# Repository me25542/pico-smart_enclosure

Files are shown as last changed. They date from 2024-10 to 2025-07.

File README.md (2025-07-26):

# pico-smart_enclosure
### Automatic active temperature control and lighting for a 3d printer enclosure.
Uses a raspberry Pi Pico connected to the printer via I2C to provide **automatic** active temperature control and full control of other enclosure functions via gcode (M260). 
Also gives full control via an OLed screen UI.

## Features
- **Automatic active temperature control**
- **Direct communication with the printer** (via I2C)
- **Smooth PWM lighting control**
- **Power loss recovery** (will save setting changes and state on power loss)
- **UI via OLed**
- Print name display while printing
- Fan kickstarting
- PWM fan speed control
- Printer-controllable max fan speed
- Motorized fan flap control
- Print done notification (light turns on)
- Use of the standby capabilities on ATX PSUs to save power
- Uses both cores in the pico for smoother real-time operation
- Highly customizable
- Light turns on when the door opens (if setting enabled)
- Control via:
    - UI - full control (except for print name), plus settings
    - M260 gcode commands (printer) - full control
    - USB connected computer - partial control (all but print name)
    - Two quick-acess buttons - changing light state and setting mode to cooldown only
- **Safety** features:
    - Fans and heaters turn off when door open
    - Sensor connection status is regularly checked
    - Sensor data is checked for plausibility (is it way to low, etc.)
    - Temperature exceeding set thresholds will cause shutdown (see below)
    - Will enter a safe "error" state if anything is wrong (invalid printer command, sensor disconnected, temp exceeds set bounds, etc.)
        - Turns off heaters
        - Turns off fans
        - Turns off lights
        - Turns off the power supply
        - Stops communication with printer
        - Sends data about the error via USB every 30 seconds, indefinitely

## To use
- **If you don't need to change anything in the code (if your hardware is the same as mine):**
	- Double check your wiring
        - Couldn't hurt, for what mine looks like see the wiring diagram below
        - Your switches can be either `NO` or `NC`, the code will detect this
    - **Ensure that whenever you upload a new version, the door is open (no switches are pressed)**
	- Plug the Raspberry Pi Pico into your computer while holding down the BOOTSEL button, copy [the latest .uf2 file](https://github.com/me25542/pico-smart_enclosure/releases) to the pico
	- Enjoy!
- **If you want to customize things in the code:**
	- I recommend Using Arduino IDE, as that is what I used and I know it works
	- Install [this](https://github.com/earlephilhower/arduino-pico) board in Arduino IDE
	    - The link has good instructions, just scroll down a bit
	- Install all dependencies (see documentation)
	- Download the files in "src/Printer_enclosure_firmware" and open them in Arduino IDE
	- Change any values as needed, depending on your setup
	- Double check your wiring (couldn't hurt, for what mine looks like see the wiring diagram below)
	- Upload the code to your Pico (see above)
	- Enjoy!

- **For wiring diagram, BOM, etc., see the documentation**

## Printer compatibility
**This design is compatible with any printer that supports [M260](https://reprap.org/wiki/G-code#M260:_i2c_Send_Data) gcode commands and has an I2C bus that you can connect to.**

The only printers that I am *certain* will work with this are the Original Prusa MK4-series printers (I made this for my MK4), as their Xbuddy board has an I2C connector that is unused. (a female 4-pin Molex Click-Mate if you want to buy a cable to fit)

**Known compatible printers:**
- Prusa MK4(s)
- Prusa MK3.9(s)
- Prusa MK3.5(s)

However, many other printers *might* have I2C connectors, so it's worth checking yours. If you find other printers that are compatible, please let me know!

A raspberry Pi might also work (they have I2C) if you are using one for Octoprint or Klipper already, with a bit of modification.

## Contribution
If you want to contribute in any way, feel free to do so!

Whether it's reporting bugs or writing code, your contributions will be helpful.

### Ideas for features to add
- Thermal runaway protection
    - protect heaters from thermal runaway
- Audible notification for print done
    - Play a small chime or sound when the print is set to done
- Support for basic control through printer GPIO pins (for printers without I2C)
    - Have a small number of pins be able to, say, set the temperature to one of two states
    - Cut out any unneeded functionality (like setting the lights, fine temperature control, etc.)
- Anything else you can think of!
    - If you can, implement it!
    - If you can't, raise an issue requesting the feature

Thank you for any and all contributions!

---

**OK, I saved the story for the end 😉.**

I couldn't find code for a smart printer enclosure that had all the features I wanted. 
Mainly, I wanted something that was automatic; I didn't want to have to set fans, heaters, etc. *every single print**. 
So, I spent a lot of time making this. 
I believe it is the most fully featured codebase for a 3d printer enclosure you could find, mainly because I couldn't find a more fully featured one.

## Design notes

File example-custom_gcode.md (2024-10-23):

## example custom gcode:

(compatible with any PrusaSlicer-based slicer)
- Prusa Slicer
- Bambu Studio
- Orca Slicer
- Super Slicer

This start gcode is based off of commands compatible with v1.1.0

List of compatible versions:
- 1.1.0
- 1.1.1
- 1.2.0

It should also be compatible with any v1.x version later than this

### Start gcode:

(add at the *verry* start of your printer's start gcode)

```
; start of my custom stuff:
M260 A8 ; set adress to 8
M260 B3 ; set enclosure mode to printing
M260 B5 ; set print not done
{if filament_type[initial_tool]=="PLA"}
M260 B15 ; set target enclosure temp to 15deg C
{elsif filament_type[initial_tool]=="PETG"}
M260 B30 ; set target enclosure temp to 30deg C
M260 B102 ; set max enclosure fan speed to 50%
{elsif filament_type[initial_tool]=="ASA"||filament_type[initial_tool]=="ABS"}
M260 B50 ; set target enclosure temp to 50deg C
M260 B100 ; set max enclosure fan speed to 0%
{elsif filament_type[initial_tool]=="FLEX"}
M260 B25 ; set target enclosure temp to 25deg C
{elsif filament_type[initial_tool]=="PC"}
M260 B50 ; set target enclosure temp to 50deg C
M260 B100 ; set max enclosure fan speed to 0%
{elsif filament_type[initial_tool]=="PA"||filament_type[initial_tool]=="NYLON"}
M260 B50 ; set target enclosure temp to 50deg C
M260 B100 ; set max enclosure fan speed to 0%
{endif}
M260 S ; send the current buffer
; end of my custon stuff
```

### End gcode

(add at the *verry* end of your printer's end gcode)

```
; start of my custom stuff:
M260 A8 ; set adress to 8
M260 B20 ; set target enclosure temp to 20deg C
M260 B2 ; set enclosure mode to cooldown
M260 B4 ; set print done
M260 S ; send the current buffer
; end of my custom stuff
```

### See also:

[RepRap - M260](https://reprap.org/wiki/G-code#M260:_i2c_Send_Data)

[Macros | Prusa knowledge base](https://help.prusa3d.com/article/macros_1775)

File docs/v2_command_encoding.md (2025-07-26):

# I2C command encoding

The encoding of commands to the enclosure into bytes sent via I2C is a bit more complicated in v2 than in v1. 
Instead of a rudimentary system where each possible byte is mapped to a command (e.g. `46` sets the target enclosure temp to 46 degrees), 
commands are encoded as a series of bytes. Each v2 command consists of at least 3 bytes: the command type, the number of bytes, and the data. 
The command structure is like this (first sent bytes on the left):

`command type`  |`number of data bytes` |`data bytes`
---             |---                    |---
^ first sent    |^ second sent          |^ last sent

The command type indicates *what* is being set. 
Currently, the only valid command types are `0xFF` to `0xF7` (`255` to `247`). 
These set different things:

Hex     |Dec    |Command type
---     |---    |---
`0xFF`  |`255`  |mode
`0xFE`  |`254`  |set temp
`0xFD`  |`253`  |print done
`0xFC`  |`252`  |max fan speed
`0xFB`  |`251`  |light state
`0xFA`  |`250`  |print name
`0xF9`  |`249`  |control mode
`0xF8`  |`248`  |heaters
`0xF7`  |`247`  |fan

The number of data bytes indicates how many data bytes are contained in the command
(e.g. if there are two data bytes this byte would be `0x02` (`2`), eighteen data bytes would make this `0x12` (`18`), etc.).

The data bytes contain the actual command data. 
What this data does / how it is encoded depends on the command type.

## Data byte actions by command type:

### Mode (`0xFF` hex, `255` dec):

Hex     |Dec    |Action
---     |---    |---
`0x00`  |`0`    |mode to error
`0x01`  |`1`    |mode to standby
`0x02`  |`2`    |mode to cooldown
`0x03`  |`3`    |mode to printing
(other) |(other)|ignored

<br>

### Set temp (`0xFE` hex, `254` dec):

Hex     |Dec    |Action
---     |---    |---
`0x00`  |`0`    |set temp to 0 (deg. c.)
`0x01`  |`1`    |set temp to 1
...     |...    |...
`0x4A`  |`74`   |set temp to 74
`0x4B`  |`75`   |set temp to 75
(other) |(other)|ignored

<br>

### Print done (`0xFD` hex, `253` dec):

Hex     |Dec    |Action
---     |---    |---
`0x00`  |`0`    |print not done
`0x01`  |`1`    |print done
(other) |(other)|ignored

<br>

### Max fan speed (`0xFC` hex, `252` dec):

Hex     |Dec    |Action
---     |---    |---
`0x00`  |`0`    |max fan speed to 0/255
`0x01`  |`1`    |max fan speed to 1/255
...     |...    |...
`0xFE`  |`254`  |max fan speed to 254/255
`0xFF`  |`255`  |max fan speed to 255/255

<br>

### Light state (`0xFB` hex, `251` dec):

Hex     |Dec    |Action
---     |---    |---
`0x00`  |`0`    |lights on
`0x01`  |`1`    |lights off
`0x02`  |`2`    |lights change
(other) |(other)|ignored

<br>

### Print name (`0xFA` hex, `250` dec):

This one is a bit different. Basically, each data byte represents one ASCII-encoded character in the print name. 
Each of these characters are added, one at a time, to the print name in place of the first `NULL`. 
The print name is full of `NULL`s when empty, so basically each character is added to the end of the part of the name that is already there.

#### Notes: 

The print name is cleared after each print automatically (when the mode returns to `standby`).
The print name has a 256-character limit, characters added after it is full will change the last character.

<br>

### Control mode (`0xF9` hex, `249` dec):

Hex     |Dec    |Action
---     |---    |---
`0x00`  |`0`    |undefined; do not use
`0x01`  |`1`    |control mode to temperature
`0x02`  |`2`    |control mode to manual
(other) |(other)|ignored

<br>

### Heaters (`0xF8` hex, `248` dec):

Hex     |Dec    |Action
---     |---    |---
`0x00`  |`0`    |heater off
`0x01`  |`1`    |heater on
(other) |(other)|ignored

#### Note:

Do not use unless the control mode is set to manual, otherwise behavior is undefined

<br>

### Fan (`0xF7` hex, `247` dec):

Hex     |Dec    |Action
---     |---    |---
`0x00`  |`0`    |fan to 0/255
`0x01`  |`1`    |ignored
`0x02`  |`2`    |fan to 2/255
`0x03`  |`3`    |ignored
...     |...    |...
`0xFC`  |`252`  |fan to 252/255
`0xFD`  |`253`  |ignored
`0xFE`  |`254`  |fan to 254/255
`0xFF`  |`255`  |ignored

#### Note:

If the least significant bit is `1`, the byte will be ignored

<br>

### Gcode examples:

#### Setting mode to `printing`:

<details>
<summary> expand </summary>

```
M260 A8 ; Address 8
M260 B255 ; Mode
M260 B1 ; 1 Byte
M260 B3 ; Printing
M260 S ; Send buffer
```

</details>

---

#### Setting a long name:

<details> 
<summary> expand </summary>

```
M260 A8 ; Address 8

; First I2C transaction (32 bytes total)
; Send the first part of the name (30 bytes)
M260 B250 ; Print name
M260 B30 ; 30 Bytes

M260 B84 ; 'T'
M260 B104 ; 'h'
M260 B105 ; 'i'
M260 B115 ; 's'
M260 B32 ; ' '
M260 B105 ; 'i'
M260 B115 ; 's'
M260 B32 ; ' '
M260 B97 ; 'a'
M260 B32 ; ' '
M260 B118 ; 'v'
M260 B101 ; 'e'
M260 B114 ; 'r'
M260 B121 ; 'y'
M260 B32 ; ' '
M260 B108 ; 'l'
M260 B111 ; 'o'
M260 B110 ; 'n'
M260 B103 ; 'g'
M260 B32 ; ' '
M260 B110 ; 'n'
M260 B97 ; 'a'
M260 B109 ; 'm'
M260 B101 ; 'e'
M260 B32 ; ' '
M260 B116 ; 't'
M260 B111 ; 'o'
M260 B32 ; ' '
M260 B116 ; 't'
M260 B101 ; 'e'

M260 S ; Send buffer

; Second I2C transaction (27 bytes total)
; Send the remaining part of the name (25 bytes)
M260 B250 ; Print name
M260 B26 ; 26 Bytes

M260 B115 ; 's'
M260 B116 ; 't'
M260 B32 ; ' '
M260 B115 ; 's'
M260 B116 ; 't'
M260 B117 ; 'u'
M260 B102 ; 'f'
M260 B102 ; 'f'
M260 B46 ; '.'
M260 B32 ; ' '
M260 B84 ; 'T'
M260 B101 ; 'e'
M260 B115 ; 's'
M260 B116 ; 't'
M260 B44 ; ','
M260 B32 ; ' '
M260 B116 ; 't'
M260 B101 ; 'e'
M260 B115 ; 's'
M260 B116 ; 't'
M260 B44 ; ','
M260 B32 ; ' '
M260 B116 ; 't'
M260 B101 ; 'e'
M260 B115 ; 's'
M260 B116 ; 't'

M260 S ; Send buffer
```

</details>

---

#### Manually turning heater on:

<details>
<summary> expand </summary>

```
M260 A8 ; Address 8
M260 B249 ; Control mode to manual
M260 B1 ; 1 Byte
M260 B248 ; Heater
M260 B1 ; Heater on
M260 S ; Send buffer
```

</details>

<br>

## Notes:

**On command length / why this encoding:**

Many commands only require one data byte, but some (like setting the print name) require more. 
Hence the byte indicating the number of data bytes.

---

**On addresses:**

The I2C address of the enclosure by default is `0x08` in hex, or `8` in dec. This can be changed by modifying a macro in the source code.

---

**On v1 compatibility:**

To maintain compatibility with v1, if the `command type` byte is in the range of `0x00` - `0x68` (`0` - `104`), it will be parsed as if it is a v1 command.
v1 commands were only one byte long, so if this is the case the next command is assumed to start with the next byte.
This means that valid v1 commands *are* still fully supported, and can be mixed with v2 commands in a given transmission.
However, it is recommended to use only v2 commands, as support for v1 commands is not guaranteed indefinitely.

---

**On maximum transmission length:**

The Marlin core used by the Prusa Buddy firmware has a limited I2C buffer size of 32 bytes; if you are sending many or long commands you may need to split them into multiple transmissions.
Additionally, the enclosure code has only a 32-byte primary buffer for incoming data, so longer transmissions wouldn't work. 
However, this buffer is flushed to a 256-byte circular buffer nearly immediately, so consecutive commands of up to 32 bytes should be fine. 
If you need more than 32 bytes, split it into multiple transmissions.

---

**If you still have questions, or this document is incomplete, please submit an issue.**

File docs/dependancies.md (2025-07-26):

## This program has several dependencies you will need to install if you want to compile it yourself:

**Mainly, you will need to install the [earlephilhower / Arduino-pico core](https://github.com/earlephilhower/arduino-pico).** This provides both the ability to compile code for the Pico, and several dependencies like:
  - stdlib
  - Wire
  - Servo
  - EEPROM
  - mutex

---

[How to install the Arduino-pico core](https://github.com/earlephilhower/arduino-pico/blob/master/docs/install.rst)

---

**Other libraries that need to be installed include:**
- [Adafruit MCP9808](https://github.com/adafruit/Adafruit_MCP9808_Library)
- [Adafruit GFX Library](https://github.com/adafruit/Adafruit-GFX-Library)
- [Adafruit SSD1306](https://github.com/adafruit/Adafruit_SSD1306)
- [Bounce2](https://github.com/thomasfredericks/Bounce2)
- Some of these have dependencies of their own, just select "install all" when prompted in arduino IDE

---

Happy compiling!

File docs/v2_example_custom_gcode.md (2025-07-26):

## v2 example custom gcode:

(compatible with any PrusaSlicer-based slicer)
- Prusa Slicer
- Bambu Studio
- Orca Slicer
- Super Slicer

**This example gcode is based off of commands compatible with v2.0.0_rc1 (internal, prerelease)**

List of compatible versions:
- v2.0.0_rc1 (internal, prerelease)
- v2.x

It should also be compatible with any v2.x versions in the future

### Start gcode:

(add at the *very* start of your printer's start gcode)

<details>

<summary> expand </summary>

```
; start of my custom stuff:
M260 A8 ; set address to 8
M260 B255 ; setting: mode
M260 B1 ; 1 byte
M260 B3 ; mode: printing
M260 B253 ; setting: print done
M260 B1 ; 1 byte
M260 B0 ; print done: false
{if filament_type[initial_tool]=="PLA"}
M260 B254 ; setting: enclosure temp
M260 B1 ; 1 byte
M260 B15 ; enclosure temp: 15deg
M260 S ; send the current buffer
{elsif filament_type[initial_tool]=="PETG"}
M260 B254 ; setting: enclosure temp
M260 B1 ; 1 byte
M260 B30 ; enclosure temp: 30 deg C
M260 B252 ; setting: max fan speed
M260 B1 ; 1 byte
M260 B127 ; max fan speed: 50%
M260 S ; send the current buffer
{elsif filament_type[initial_tool]=="ASA"||filament_type[initial_tool]=="ABS"}
M260 B254 ; setting: enclosure temp
M260 B1 ; 1 byte
M260 B50 ; enclosure temp: 50 deg C
M260 B252 ; setting: max fan speed
M260 B1 ; 1 byte
M260 B0 ; max fan speed: 0%
M260 S ; send the current buffer
{elsif filament_type[initial_tool]=="FLEX"}
M260 B254 ; setting: enclosure temp
M260 B1 ; 1 byte
M260 B25 ; enclosure temp: 25 deg C
M260 S ; send the current buffer
{elsif filament_type[initial_tool]=="PC"}
M260 B254 ; setting: enclosure temp
M260 B1 ; 1 byte
M260 B50 ; enclosure temp: 50 deg C
M260 B252 ; setting: max fan speed
M260 B1 ; 1 byte
M260 B0 ; max fan speed: 0%
M260 S ; send the current buffer
{elsif filament_type[initial_tool]=="PA"||filament_type[initial_tool]=="NYLON"}
M260 B254 ; setting: enclosure temp
M260 B1 ; 1 byte
M260 B50 ; enclosure temp: 50 deg C
M260 B252 ; setting: max fan speed
M260 B1 ; 1 byte
M260 B0 ; max fan speed: 0%
M260 S ; send the current buffer
{endif}
; end of my custom stuff
```

</details>

---

### End gcode

(add at the *very* end of your printer's end gcode)

<details>

<summary> expand </summary>

```
; start of my custom stuff:
M260 A8 ; set address to 8
M260 B254 ; set temp
M260 B1 ; 1 byte
M260 B20 ; 20 deg. c
M260 B255 ; mode
M260 B1 ; 1 byte
M260 B2 ; cooldown
M260 B253 ; print done
M260 B1 ; 1 byte
M260 B1 ; set print done
M260 S ; send the current buffer
; end of my custom stuff
```

</details>

---

### See also:

[RepRap - M260](https://reprap.org/wiki/G-code#M260:_i2c_Send_Data)

[Macros | Prusa knowledge base](https://help.prusa3d.com/article/macros_1775)

Make sure to read the documentation on command encoding.

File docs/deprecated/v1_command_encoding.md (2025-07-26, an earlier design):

# v1 commands are deprecated, use v2 instead

**This is only included for archival reasons**

---

## Received I2C values, and what they do:

**Values 0-3 set the enclosure mode:**
- 0 = error (shuts everything down and enters a safe state)
- 1 = standby (doesn't really do anything, turns off the PSU to save power when the lights are off)
- 2 = cooldown (turns on the vent fan until the enclosure temp is close enough to the outside temp)
- 3 = printing (maintains the target temperature by heating or cooling as is required)

**Values 4-9 set other things:**
- 4 = print done
- 5 = print not done
- 6 = turns enclosure lights on
- 7 = turn enclosure lights off
- 8 = changes enclosure lights state (from off to on and vice versa)
- 9 = reserved for future use (sets mode to error)
	
**Values 10-99 set target temp:**
- 10 = target temp of 10 °C
- 11 = target temp of 11 °C
- ...
- 98 = target temp of 98 °C
- 99 = target temp of 99 °C

**Values 100-104 set max fan speed:**
- 100 = max fan speed of 0% (vents will still be opened)
- 101 = max fan speed of 25%
- 102 = max fan speed of 50%
- 103 = max fan speed of 75%
- 104 = max fan speed of 100%

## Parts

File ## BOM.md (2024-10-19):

## BOM

(In no particular order):
- 1x 3d printer enclosure
- 1x ATX power supply (anything over ~250w will work)
- 1x Raspberry Pi Pico
- 1x heater
	- 2x 50w 3Ω power resistors
	- 1x old computer heatsink w. 12v fan
- 1x 5v relay module (at least one channel)
- 2x generic logic level converters (the "bad" kind)
- 2x 5v 9g servos
- 3x MCP9808 sensors
- 3x micro switches
- 4x BC337 transistors
- 4x 1kΩ resistors
- 4x 220Ω
- 4x white 5mm LEDs
- Some 12v white LED strips
- Some sort of connector to plug into your printer's control board (Molex Click-Mate for a MK4)
- Probably some other little things that I forgot. Use common sense.

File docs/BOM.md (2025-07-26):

## BOM

(In no particular order):
- 1x 3d printer enclosure
- 1x ATX power supply (anything powerful enough for your heater will work)
- 1x Raspberry Pi Pico
- 1x ssd1306-based OLed display with I2C support (the UI is optimized for the ones with a rectangle of yellow pixels at the top)
- 1x 12v heater
- 1x 5v relay module (at least one channel)
- 1x 220Ω resistor
- 1x 5mm LED
- 2x generic logic level converters (the "bad" kind)
- 2x 5v 9g servos
- 3x MCP9808 sensors
- 3x micro switches
- 3x push-button switches
- 4x BC337 transistors
- 4x 1kΩ resistors
- Some 12v white LED strips
- Some sort of connector to plug into your printer's control board (4 pin Molex Click-Mate for a MK4)
- Probably some other little things that I forgot. Use common sense.

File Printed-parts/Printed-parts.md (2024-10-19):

## You will probably want to print some parts for your enclosure

### Some things you might want to print include:
- PSU holder
- Indicator light holder
- Switch (button) holders
- Relay board holder
- Heater mount

I plan to include the files for what I used for some of these, but others might also work.

[This](https://www.printables.com/@_me_/collections/1713789) is an up-to-date list of the printed parts I used for my enclosure

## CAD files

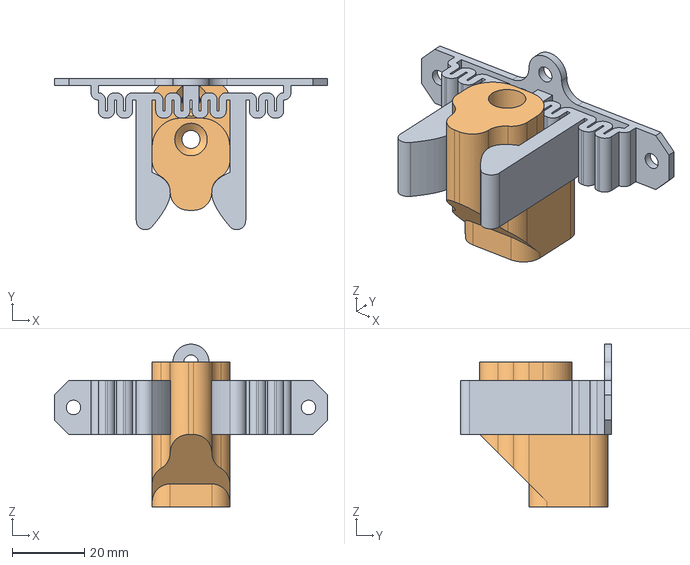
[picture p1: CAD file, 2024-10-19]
Printed-parts/latch v8.step
75.5 x 41.9 x 45.0 mm

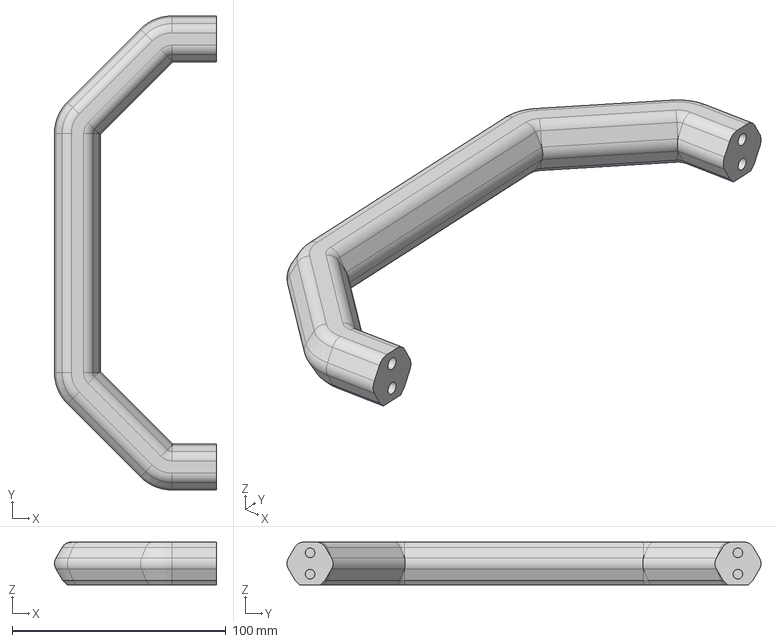
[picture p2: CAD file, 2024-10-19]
Printed-parts/handel v4.step
75.8 x 221.5 x 20.0 mm

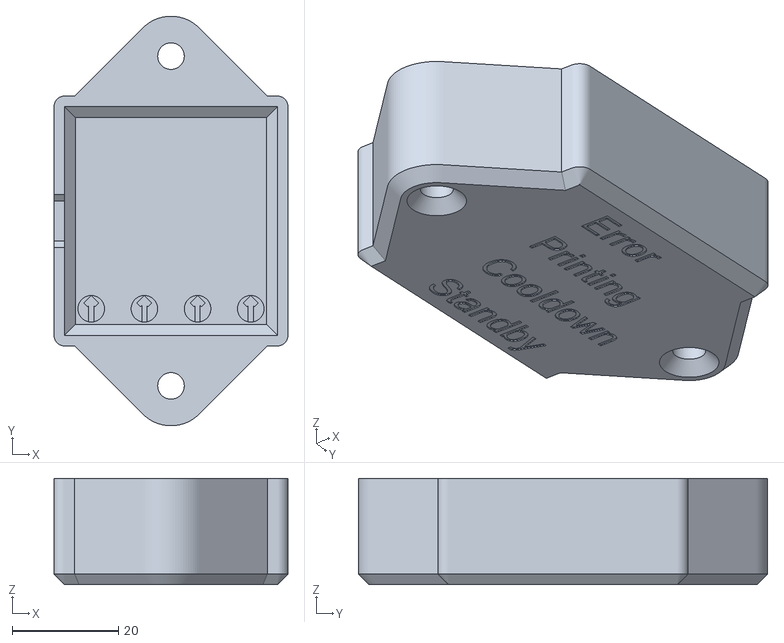
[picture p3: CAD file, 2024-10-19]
Printed-parts/mode_indicator.stl
44.0 x 77.0 x 20.0

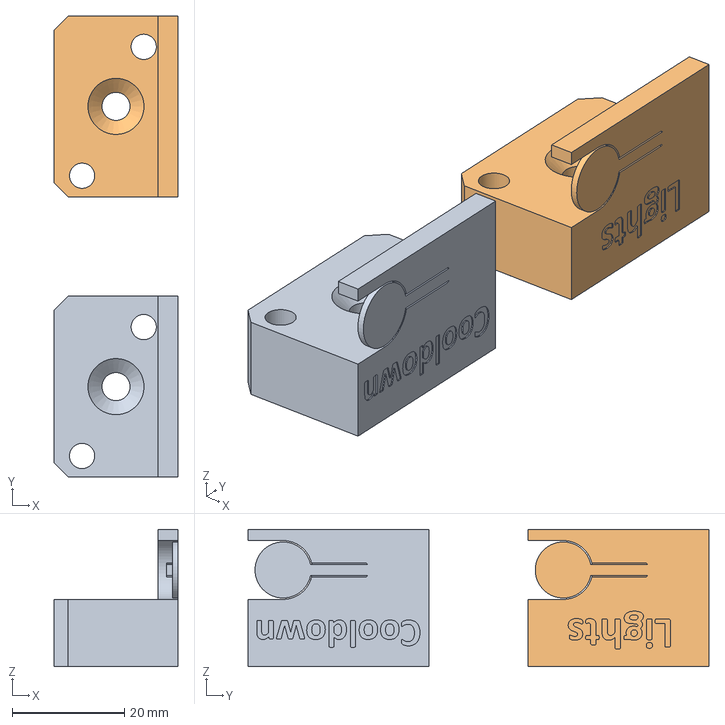
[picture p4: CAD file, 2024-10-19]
Printed-parts/enclosure_micro-switch_button v6.step
22.1 x 82.3 x 24.5 mm

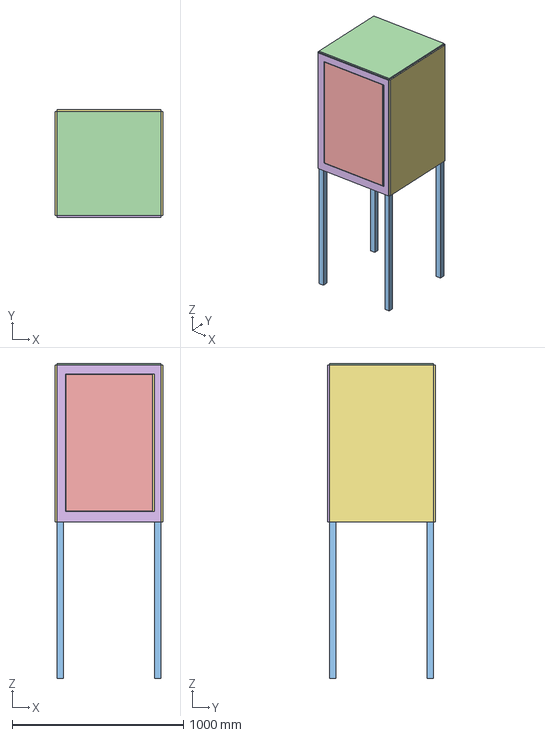
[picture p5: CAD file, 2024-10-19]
Printed-parts/3d_printer_enclosure_v3 v6.step
628.6 x 628.6 x 1838.3 mm

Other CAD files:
Printed-parts/mode_indicator v1.step
Printed-parts/enclosure_micro-switch_button v6.stl
Printed-parts/handel v4.stl
Printed-parts/latch v8.stl

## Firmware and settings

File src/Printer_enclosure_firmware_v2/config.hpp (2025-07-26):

/**
* @file config.hpp
* @brief main config file
*/

/*
 * Copyright (c) 2024-2025 Dalen Hardy
 * 
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
 * THE SOFTWARE IS PROVIDED "AS IS", WITHOUT WARRANTY OF ANY KIND, EXPRESS OR
 * IMPLIED, INCLUDING BUT NOT LIMITED TO THE WARRANTIES OF MERCHANTABILITY,
 * FITNESS FOR A PARTICULAR PURPOSE AND NONINFRINGEMENT. IN NO EVENT SHALL THE
 * AUTHORS OR COPYRIGHT HOLDERS BE LIABLE FOR ANY CLAIM, DAMAGES OR OTHER
 * LIABILITY, WHETHER IN AN ACTION OF CONTRACT, TORT OR OTHERWISE, ARISING FROM,
 * OUT OF OR IN CONNECTION WITH THE SOFTWARE OR THE USE OR OTHER DEALINGS IN THE
 * SOFTWARE.
*/

#pragma once

#include "constants.hpp"
#include <Arduino.h>

#define DEBUG true // sets if debug messages will be sent. set to "true" for debuging messages, and to "false" for none (except if there is an error)
#define SERIAL_CONTROL false // sets if serial control will be used, and thus if serial should be initialized at the start of the program if debug is false

// version info (e.g. 1.2.3 : majorV. = 1, minorV. = 2, bugFixV. = 3)
constexpr uint8_t majorVersion = 2;
constexpr uint8_t minorVersion = 1;
constexpr uint8_t bugFixVersion = 0;
constexpr uint8_t buildVersion = 18; // this might be useful if you make your own changes to the code

// other

#define MANUAL_PRESSED_STATE false // are you seting the pressed state of the switches manually, or automatically?

#define WATCHDOG_TIME 5000 // the loop time (in milliseconds) of either core at or above which error mode will be entered

#define LED_ON_TIME 100 // the time (in milliseconds) the led will be on for when blinking (not in error mode)
#define LED_OFF_TIME_STANDBY 4900 // the time (in milliseconds) that the LED will stay off for when blinking and the mode is standby
#define LED_OFF_TIME_OTHER 900 // the time (in milliseconds) that the LED will stay off for when blinking and the mode is not standby (or error)

#define MIN_SET_TEMP 5
#define MAX_SET_TEMP 75
#define DEFAULT_SET_TEMP 20

#define MAX_SERIAL_STARTUP_TRIES 1000 // the number of tries (or the number of 10ms periods) that will be taken to connect to USB before giving up
#define MAX_SCREEN_STARTUP_TRIES 100 // the number of times that turning the screen on will be tried
#define MAX_PSU_ON_TIME 10000 // the maximum time (in milliseconds) that the PSU can take to turn on before throwing an error
#define MAX_OTHER_CORE_SHUTDOWN_TIME 2500 // the maximum time (in milliseconds) that the first core will wait for the second core (core1) to acknowledge an error and shut down before proceeding anyways

#define MAX_IN_OUT_TEMP 75 // the maximum temp the inside or outside of the enclosure can be before triggering an error
#define MAX_HEATER_TEMP 90 // the maximum temp the heater can reach before triggering an error
#define MIN_TEMP 0 // the minimum temp any of the sensors can read before triggering an error

#define ERROR_FIX_INTERVAL 3600000 // the time (in miliseconds) after reboot when it will be forgoten if the reboot was to fix an error
#define MAX_I2C_WAIT_TIME 10000000 // the maximum time (in microseconds) to wait for I2C resources to be available
#define ENCLOSURE_ADDRESS 0x08 ///< the I2C address of the enclosure (what address the printer can connect to)
#define SERIAL_TIMOUT 100 // the serial timout time, in miliseconds

#define MENU_SELLECTED_INDICATOR ">" // MUST BE ONLY ONE CHARACTER!

#define USE_DEFAULT_DEBOUNCE_TIME false // if default Bounce2 stable interval time (10ms) is to be used

#if !USE_DEFAULT_DEBOUNCE_TIME
#define DOOR_SWITCH_DEBOUNCE_TIME 50
#define LIGHT_SWITCH_DEBOUNCE_TIME 50
#define COOLDOWN_SWITCH_DEBOUNCE_TIME 50
#define SELL_SWITCH_DEBOUNCE_TIME 20
#define UP_SWITCH_DEBOUNCE_TIME 20
#define DOWN_SWITCH_DEBOUNCE_TIME 20
#endif

#define BOOTSEL_UPDATE_TIME 1000 ///< the interval (in milliseconds) between when the state of the BOOTSEL button is updated

#define COOLDOWN_SWITCH_HOLD_TIME 5000 ///< the time, in miliseconds, that the cooldown switch needs to be held to trigger a cooldown

#define SCREENSAVER_SPEED 7 ///< the time (in milliseconds) between changes of lit pixel when screensaver displayed

#define DEFAULT_LIGHTS_ON_ON_DOOR_OPEN true
#define DEFAULT_SAVE_STATE_ON_POWER_LOSS true

#define DEFAULT_NAME_SCROLL_SPEED 100
#define DEFAULT_MENU_SCROLL_SPEED 75

#define DEFAULT_FAN_OFF_VAL 0
#define DEFAULT_FAN_MID_VAL 128
#define DEFAULT_FAN_ON_VAL 255
#define DEFAULT_DEFAULT_MAX_FAN_SPEED 255

#define DEFAULT_HYSTERESIS 1
#define DEFAULT_BIG_DIFF 3
#define DEFAULT_COOLDOWN_DIFF 3

#define DEFAULT_DIMING_TIME 3
#define DEFAULT_PDL_DIMING_TIME 5

#define DEFAULT_I2C_TEMP_SENSOR_RES 1
#define DEFAULT_SENSOR_READS 3
#define DEFAULT_SENSOR_READ_INTERVAL 10

#define DEFAULT_SERVO1_OPEN 180
#define DEFAULT_SERVO2_OPEN 180
#define DEFAULT_SERVO1_CLOSED 0
#define DEFAULT_SERVO2_CLOSED 0
#define DEFAULT_SERVO1_SPEED 1
#define DEFAULT_SERVO2_SPEED 1

#define DEFAULT_BACKUP_INTERVAL 1
#define DEFAULT_SCREENSAVER_TIME 15
#define DEFAULT_FAN_KICKSTART_TIME 1000
#define DEFAULT_MENU_BUTTON_HOLD_TIME 750

#define DEFAULT_CONTROL_MODE CONTROL_MODE_TEMP // developmental

// hardware (depends on the hardware you use and how you wired everything)

#define FAN_ON HIGH ///< pin state at which the fan will be on
#define MAIN_LIGHTS_ON HIGH ///< pin state at which the main lights will be on
#define PRINT_DONE_LIGHT_ON HIGH ///< pin state at which the print done light will be on
#define ERROR_LIGHT_ON HIGH ///< pin state at which the error light will be on

#define HEATER_TEMP_SENSOR_ADDRESS 0x18 ///< I2C address of the heater temp sensor
#define IN_TEMP_SENSOR_ADDRESS 0x19 ///< I2C address of the in temp sensor
#define OUT_TEMP_SENSOR_ADDRESS 0x1A ///< I2C address of the out temp sensor
#define SCREEN_ADDRESS 0x3C ///< I2C address of screen | See datasheet for Address; usually 0x3D for 128x64, 0x3C for 128x32 (this code not designed with 128x32 in mind; be warned)

#define SCREEN_HEIGHT 64 ///< OLED display height, in pixels | code currently not designed for this to be changed. sorry.
#define SCREEN_WIDTH 128 ///< OLED display width, in pixels | code currently not designed for this to be changed. sorry.
#define LINE_GAP 2 // gap to be inserted between lines of text on screen, in pixels
#define LINE_SPACING (CHARACTER_HEIGHT + LINE_GAP) /// the number of pixels between the top of each line of text
#define VISIBLE_MENU_ITEMS ((SCREEN_HEIGHT - ((CHARACTER_HEIGHT * 2) - LINE_GAP)) / LINE_SPACING) // the number of menu items that are visible when the print name is not displayed

#if MANUAL_PRESSED_STATE
constexpr bool doorSw_ps = LOW;
constexpr bool lightSw_ps = LOW;
constexpr bool coolDownSw_ps = LOW;
constexpr bool sellSw_ps = LOW;
constexpr bool upSw_ps = LOW;
constexpr bool downSw_ps = LOW;
#endif

// pins (how did you wire everything up?):

#define LED_PIN LED_BUILTIN /// the pin connected to the built-in LED | output

#define SELL_SWITCH_PIN 16 /// the pin connected to the "sellect" button | input
#define UP_SWITCH_PIN 15 /// the pin connected to the "up" button | input
#define DOWN_SWITCH_PIN 14 /// the pin connected to the "down" button | input

#define SERVO_2_PIN 20 /// the pin connected to servo 1 | output
#define SERVO_1_PIN 19 /// the pin connected to servo 2 | output

#define POWER_OK_PIN 18 /// the pin connected to the PSUs P_OK pin | input

#define ERROR_LIGHT_PIN 13 /// the pin connected to the "error" mode indicator light | output
#define PRINT_DONE_LIGHT_PIN 17 /// the pin connected to the print done light | output

#define COOLDOWN_SWITCH_PIN 12 /// the pin connected to the "cooldown" switch / button | input
#define LIGHTSWITCH_PIN 11  ///  the pin connected to the "lights" switch / button | input

#define HEATER_1_PIN 10 /// the pin connected to heater 1 | output
#define HEATER_2_PIN 9 /// the pin connected to heater 2 | output

#define I2C1_SCL_PIN 7 /// this is set somewhat in hardware; be careful changing
#define I2C1_SDA_PIN 6 /// this is set somewhat in hardware; be careful changing

#define I2C0_SDA_PIN 4 /// this is set somewhat in hardware; be careful changing
#define I2C0_SCL_PIN 5 /// this is set somewhat in hardware; be careful changing

#define DOOR_SWITCH_PIN 3 /// the pin connected to the door safety switch | input
#define LIGHTS_PIN 2 /// the pin connected to the enclosure lights | output
#define PSU_ON_PIN 1 /// the pin connected to the PSUs power on pin | output
#define FAN_PIN 0 /// the pin connected to the vent fan | output

#if DEBUG
#warning "USB debuging is enabled; remember to have the host connected and active at boot"
#else
#warning "USB debuging is disabled; if USB controll is not enabled USB will only become active in the event of an error"
#endif

#if SERIAL_CONTROL
#warning "USB controll is enabled; remember to have the host connected and active at boot"
#else
#warning "USB controll is disabled; if debuging is not enabled USB will only become active in the event of an error"
#endif
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

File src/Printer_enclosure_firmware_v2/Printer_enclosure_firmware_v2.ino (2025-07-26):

 /*
 * Copyright (c) 2024-2025 Dalen Hardy
 * 
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
 * THE SOFTWARE IS PROVIDED "AS IS", WITHOUT WARRANTY OF ANY KIND, EXPRESS OR
 * IMPLIED, INCLUDING BUT NOT LIMITED TO THE WARRANTIES OF MERCHANTABILITY,
 * FITNESS FOR A PARTICULAR PURPOSE AND NONINFRINGEMENT. IN NO EVENT SHALL THE
 * AUTHORS OR COPYRIGHT HOLDERS BE LIABLE FOR ANY CLAIM, DAMAGES OR OTHER
 * LIABILITY, WHETHER IN AN ACTION OF CONTRACT, TORT OR OTHERWISE, ARISING FROM,
 * OUT OF OR IN CONNECTION WITH THE SOFTWARE OR THE USE OR OTHER DEALINGS IN THE
 * SOFTWARE.
*/

#include <Arduino.h>
#include "constants.hpp"
#include "config.hpp" // include configuration variables
#include "customLibs.hpp" // include custom helper classes (libraries)
#include "vars.hpp" // include global variables
#include "menuFuncs.hpp" // include the functions used for the menu (procesing button input, drawing the menu on the screen, etc.)
#include "otherFuncs.hpp" // Include the other functions
#include "ISRs.hpp" //  Include ISRs (Interrupt Service Routines)
#include "modeFuncs.hpp" // Include functions called based on the enclosure mode
#include "setup.hpp" // include the setup functions

//********************************************************************************************************************************************************************************

// the setup code for core0
void setup() {
  varInit();
  
  #if debug || SERIAL_CONTROL // only start serial if debuging or serial controll is enabled
  serialSetup();
  while (!Serial); // wait for a USB Host to be connected
  #endif

  core1StartStartup = true; // tell the other core to start startup

  pinSetup();

  if (!setPSU(true)) startupError = true; // try turning on the PSU

  servoSetup();

  if (!tempSensorSetup()) startupError = true; // try turning on the temp sensors

  printerI2cSetup();

  attachInterrupt(digitalPinToInterrupt(POWER_OK_PIN), losingPower, FALLING); // power loss interrupt

  #if debug
  Serial.printf("waiting for core1 to start up...\n"); // print a debug message over USB
  #endif

  while (!coreOneStartup) delayMicroseconds(1); // wait for the second core to start up

  #if debug
  Serial.printf("done waiting for core1 to start up.\n"); // print a debug message over USB
  #endif

  if (startupError) {
    #if debug
    Serial.printf("Startup failed.\n"); // print a debug message over USB
    #endif
    error();

  } else {
    #if debug
    Serial.printf("Startup sucessful.\n"); // print a debug message over USB
    #endif
    coreZeroStartup = true; // tell the other core that we have finished starting up

    digitalWrite(LED_PIN, LOW), delay(1000); // blink LED to show startup complete
    digitalWrite(LED_PIN, HIGH), delay(1000); // same thing this line
  }
}

// the setup code for core1
void setup1() {
  while (!core1StartStartup); // wait for the other core to tell us to start up

  if (menuSetup()) { // try seting up the menu
    backupRecovery(); // initialize the menu with the data stored in the simulated EEPROM, if aplicable

    buttonSetup(); // set up the buttons

  } else { // if it failed
    startupError = true; // if it failed we didn't suceed
  }

  #if debug
  Serial.printf("waiting for core0 to be done startup...\n"); // print a debug message over USB
  #endif

  do { // do this at least once:
    coreOneStartup = true; // tell the other core that we have finished starting up

    if (startupError) { // if there was an error starting up in either core
      error();
    }

    delayMicroseconds(1); // wait for a tiny bit

  } while (! coreZeroStartup); // and then repeat it while the first core hasn't started up

  #if debug
  Serial.printf("done waiting for core0 to be done startup.\n"); // print a debug message over USB
  #endif
}

//********************************************************************************************************************************************************************************

// the loop code for core0
void loop() {
  #if debug
  Serial.printf("Core 0 start of loop.\n"); // print a debug message over the sellected debug port
  #endif

  const static void (*modeFuncs[])(void) = {error, standby, cooldown, printing}; // an array of functions to call based on the mode | this will only be made the first time through the loop
  constexpr static uint8_t modeFuncCount = sizeof(modeFuncs) / sizeof(modeFuncs[0]); // find the number of mode functions (at compile, not during runtime)
  
  if (mode >= modeFuncCount) setError(2, mode, false); // enter error mode if the mode is invalid
  if (mode != MODE_ERROR) standard(); // do the stuff needed every loop, regardless of mode (if the mode isn't error)

  modeFuncs[mode](); // call the mode function coresponding to the mode

  oldMode = mode; // update the variable tracking the old mode
  oldControlMode = controlMode; // update the variable tracking the old control mode
}

// the loop code for core1
void loop1() {
  #if debug
  Serial.printf("Core 1 start of loop.\n"); // print a debug message over the sellected debug port
  #endif

  if (mode == MODE_ERROR) error();

  core1Time = millis();

  core1WatchdogTimer.set(WATCHDOG_TIME); // reset the core 1 (software) watchdog timer

  if (core0WatchdogTimer.isDone()) setError(11, 0, false); // set mode to error if the core 0 (software) watchdog timer ran out

  checkButtons(); // update the state of the switches

  checkMenuButtons(); // update the state of the menu navigation buttons

  updateScreen(); // update the screen

  printDoneLight.tick(); // update the print done light
  mainLight.tick(); // update the main lights
}

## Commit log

2024-10-18 added wiring diagram
2024-10-18 Update and rename received I2C values, and what they .txt to received I2C values, and what they .md
    changed format to markdown
2024-10-18 Update and rename received I2C values, and what they .md to received I2C values, and what they do.md
2024-10-18 Update wiring picture
2024-10-19 update enclosure wiring
2024-10-19 Update README.md
    Added Bill Of Materials
2024-10-19 Update and rename ## BOM.md to BOM.md
2024-10-19 Update README.md
    Added link to printed parts
2024-10-19 Add files via upload
    Add 3d model files
    [3d_printer_enclosure_v3 v6.step, enclosure_micro-switch_button v6.step, enclosure_micro-switch_button v6.stl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]
2024-10-19 Add files via upload
    update code to allow max fan speed to be set by printer | updated comments
2024-10-19 Update received I2C values, and what they do.md
    Update to include v1.1 commands (max fan speed control)
2024-12-13 Update files to v2.0.0_alpha3
    Bugfixes
    [ISRs.cpp, menuFuncs.cpp, modeFuncs.cpp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]
2024-12-15 Update files to v2.0.0_beta1
    Bugfixes!
    [ISRs.cpp, menuFuncs.cpp, setup.cpp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]
2024-12-21 Delete BOM.md
    was deprecated
